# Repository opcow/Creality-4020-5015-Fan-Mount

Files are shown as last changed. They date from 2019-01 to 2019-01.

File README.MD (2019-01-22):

# Ender 3 4010/4020/5015 Fan Mount and Duct

---
### Main Cooling Fan Mount
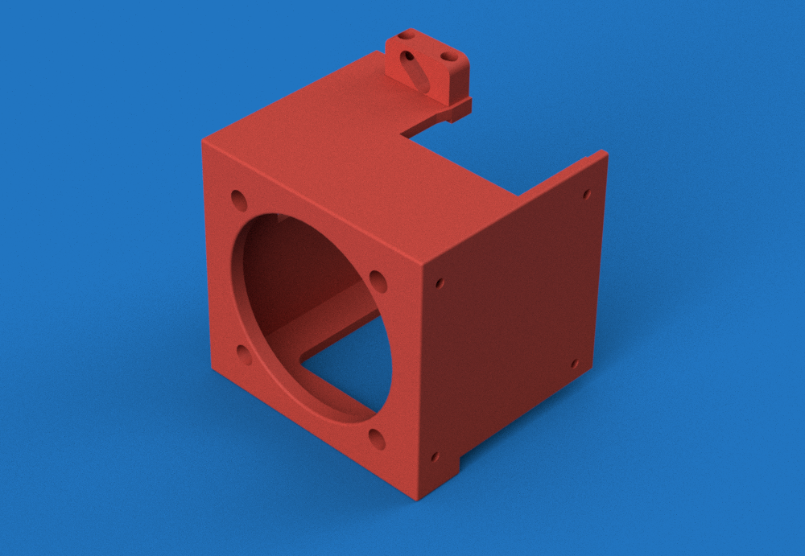
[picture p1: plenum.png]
plenum image


This part is based on the stock fan cover, but allows the use of a 4020 axial fan on Ender 3 and maybe other Creality printers for heatsink cooling. If using a 4020 fan it must mount on the outside. A 4010 fan should work mounted inside, but I haven't tried it. You can use the stock part cooler or the 5015 bracket and duct with this part (see below).

Parts needed:
* The stock heat sink cooling fan or another 4010 or 4020 axial fan. (The Ender 3 fans are 24v.)
* 2-4 M4 x 15-25mm screws depending on your fan size for mounting the fan. (I only use 2.)
* 4 M3 x 8-10MM screws.
* The original 2 M3 fan cover mounting screws or 2 more M3 x 6mm. If using a socket cap screw for the top bracket slot, a small washer may be needed.
* The original 4 part cooling fan screws or 4 M2 socket cap screws. I believe the stock screws are 2 8mm at the top and 2 10mm at the bottom (where the duct mounts).

Parts to print:

<ul>
<li>plenum_v2.stl</li>
<li>bracket_left_v2.stl</li>
<li>bracket_top_v2.stl or bracket_top_no_slot_v2.stl</li>
</ul>
  I designed this in multiple parts to avoid the need for supports. Print with the fan intake hole down. Be sure to print the left bracket with a flat side down. The non-slotted top bracket can be substitutted for the slotted version. The slotted version provides a bit of adjustment if the fan mount tilt.

Assembly:
1. Mount the top bracket to the fan housing using 2 M3 screws.
2. Mount the left bracket to the fan housing using the 2 stock M3 cover mounting screws or your own M3 screws.
3. If the screw holes are tight you may get bulges around them where the housing mounts to the metal bracket. If so, trim them and any other bumps using a razor of a file, so that the housing will mount flush with the metal plate.
4. Do the following 2 steps in whatever order works best for you. I Installed an inline connector for my 4020 fan, so I install it first and then plug it in as the last step.
5. Mount the fan to the fan housing. Make sure it is oriented so that it blows inward.
6. Mount the stock part cooling fan (don't forget its 90° duct) or the 5015 fan duct to the right side of the fan housing.
7. Mount the fan housing using M3 screws.

---

### 5015 Bracket and Duct
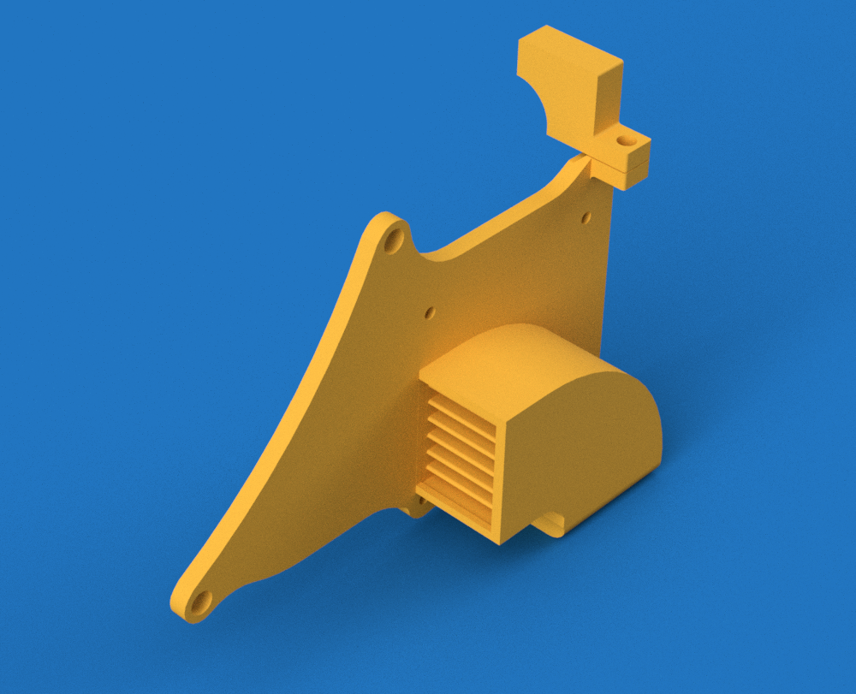
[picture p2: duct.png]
duct image

This part should also work with the stock metal fan cover. 

Parts needed:
* A 5015 centrifugal fan. (The Ender 3 fans are 24v.)
* 3 M2 screws (I used the screws for the stock part cooling fan for this).
* 1 M3 x 6-8mm screw if using the optional bracket.

Parts to print:
<ul>
<li>5015_duct_v2.stl or 5015_duct_v3.stl</li>
<li>5015_lower_duct_v3.stl or 5015_lower_duct_v3_mod.stl if using duct v3</li>
<li>duct_bracket_v2.stl</li>
</ul>

  5015_lower_duct_v3_mod.stl hangs lower and also angles the air a bit lower. 
  
  No supports are needed for the main part. The optional small bracket should be printed with supports and oriented with the slot facing upwards.

Assembly:
1. If you are using the printed main cooling fan mount, assemble it first as per above, but do not mount it to the printer.
2. Mount the duct to the right side of the main cooling fan box using 3 M2 screws.
3. Mount the entire assembly to the printer.

---
### Optional Items
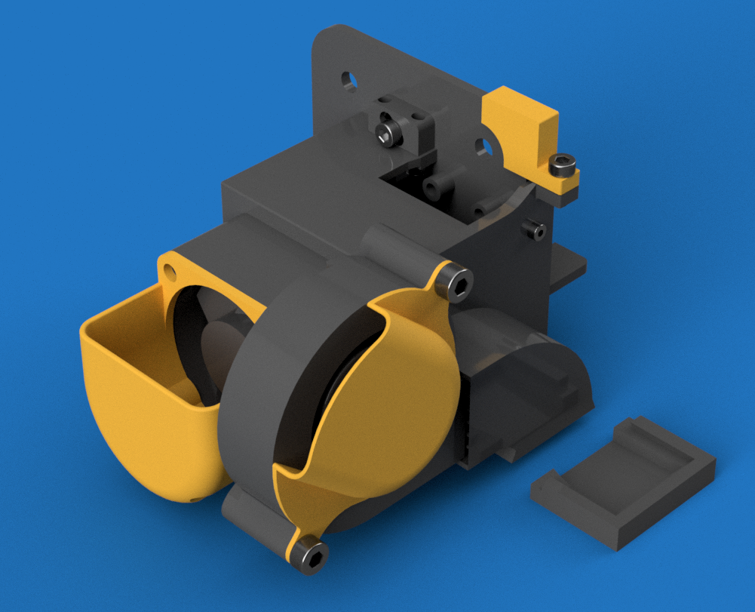
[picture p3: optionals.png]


 duct_bracket_v2.stl is an optional bracket that hooks to the hot end mounting plate. It gives the entire assembly a bit more stiffness. It won't work with the stock metal fan housing and would probably offer little to no benefit anyway.

 40_intake.stl and 50_intake.stl are optional intake ducts. They may reduce the amount of random plastic scrap getting sucked into the fans.

---
### Version 3 Duct

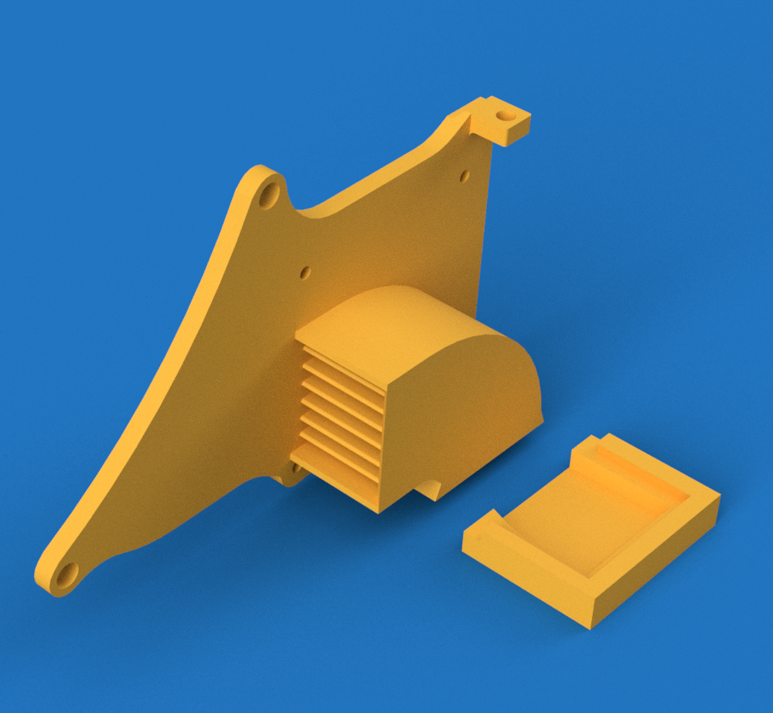
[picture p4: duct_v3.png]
duct version 3 image


Version 3 of the 5015 mount and duct uses a separate lower duct that snaps in using a dovetail joint. It may provide better airflow. Step files are included if you'd like to make your own modifications.

---

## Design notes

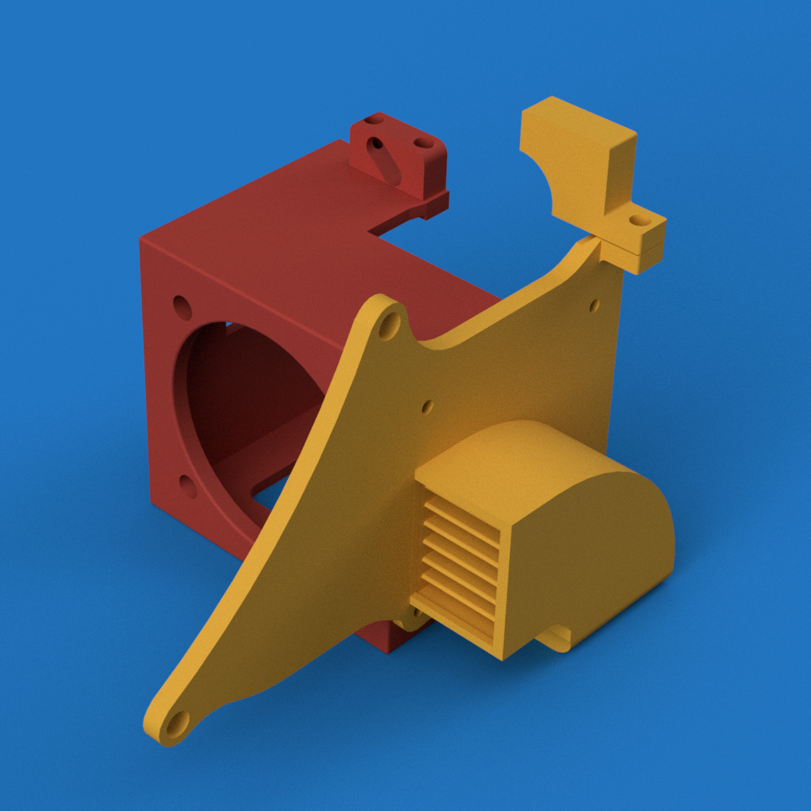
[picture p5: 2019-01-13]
view_5.png

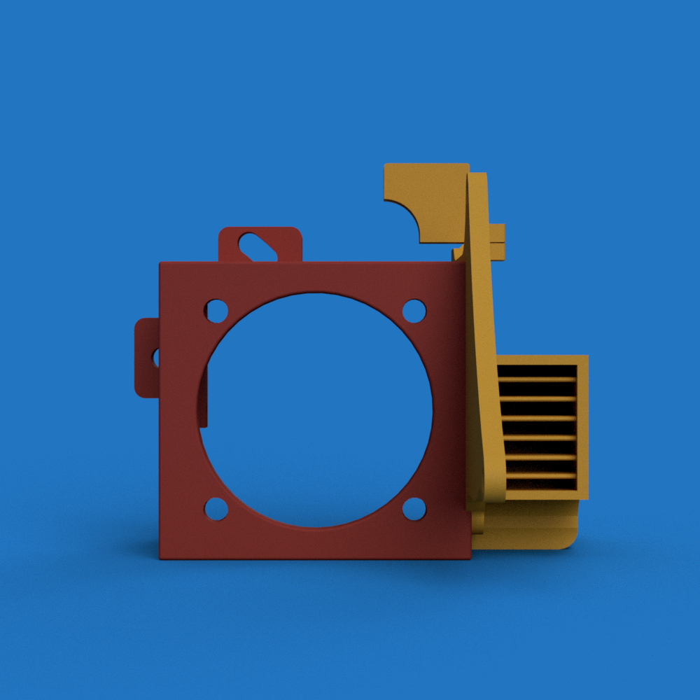
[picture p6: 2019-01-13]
view_3.png

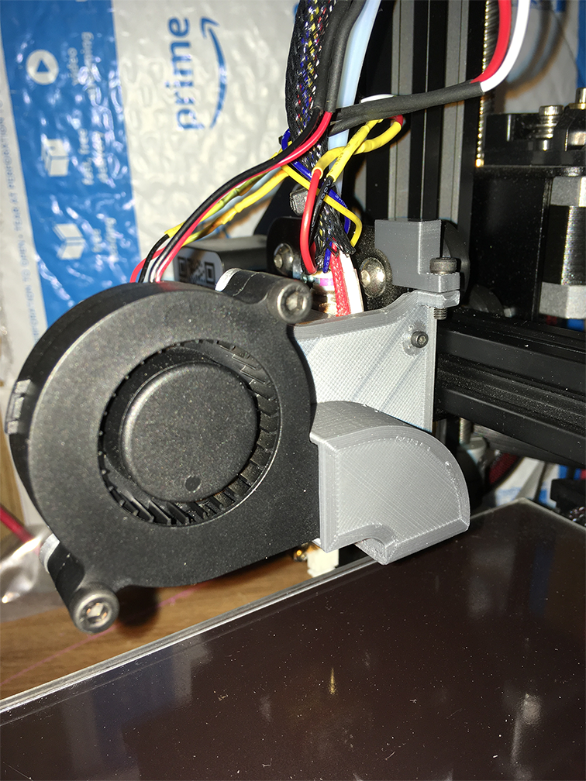
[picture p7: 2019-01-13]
snap.png

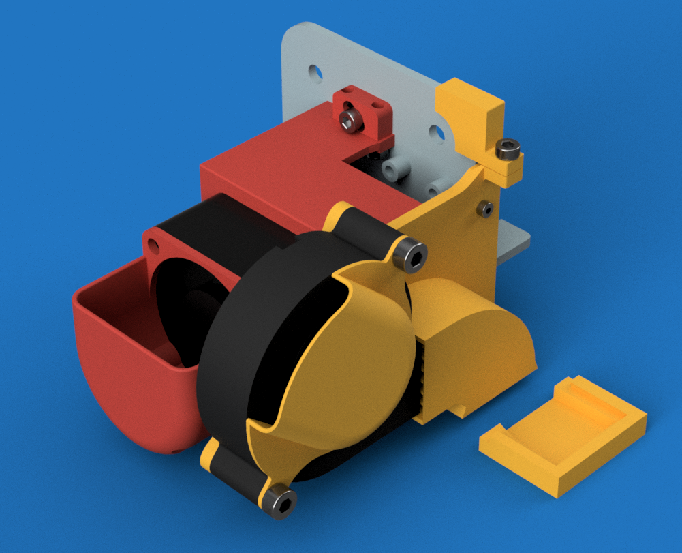
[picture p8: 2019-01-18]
view_1.png

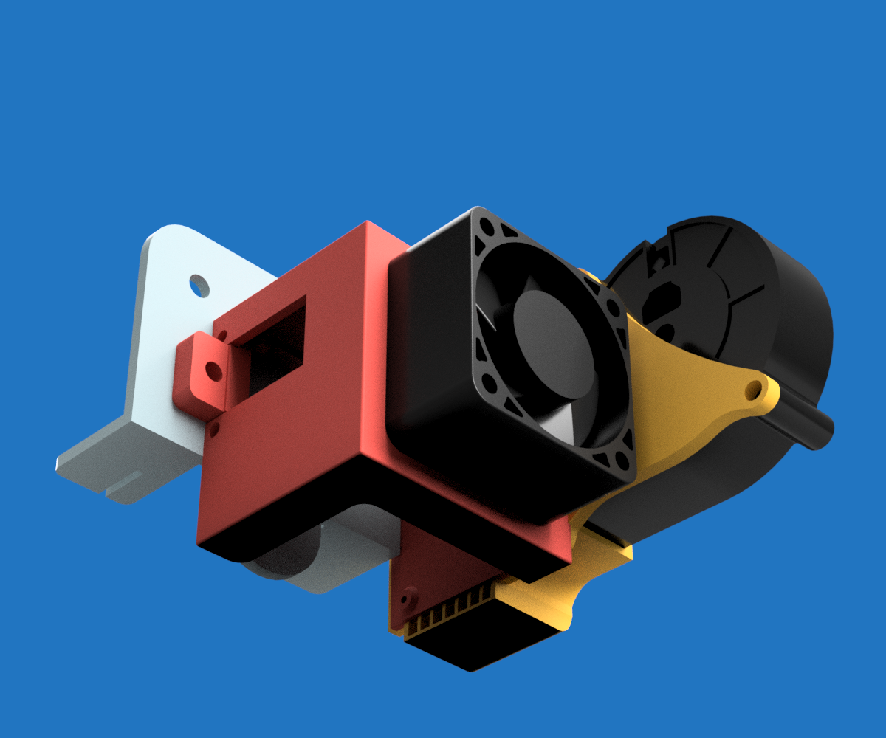
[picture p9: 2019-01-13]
view_2.png

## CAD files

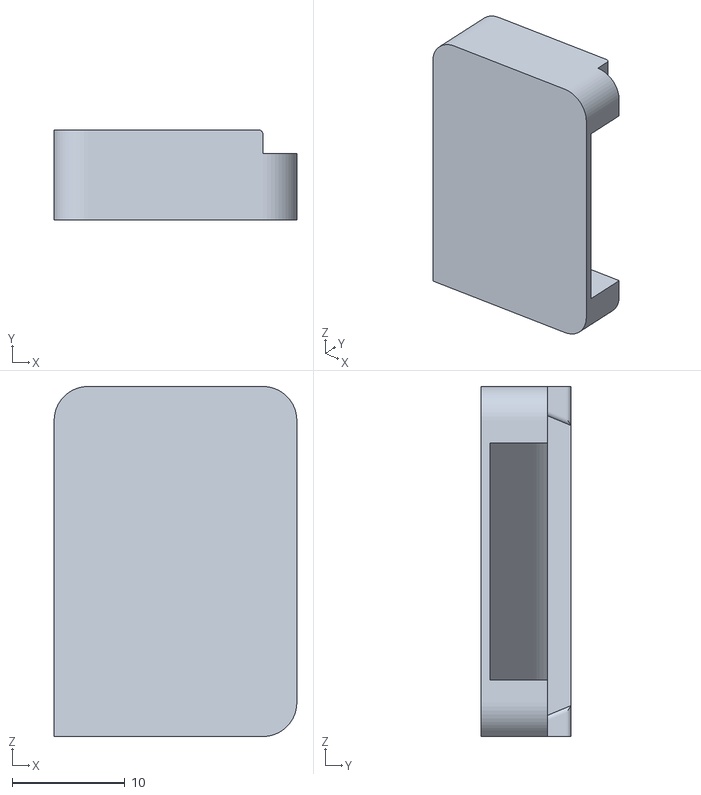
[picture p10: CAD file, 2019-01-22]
5015_lower_duct_v3_mod.stl
21.5 x 8.00 x 31.0

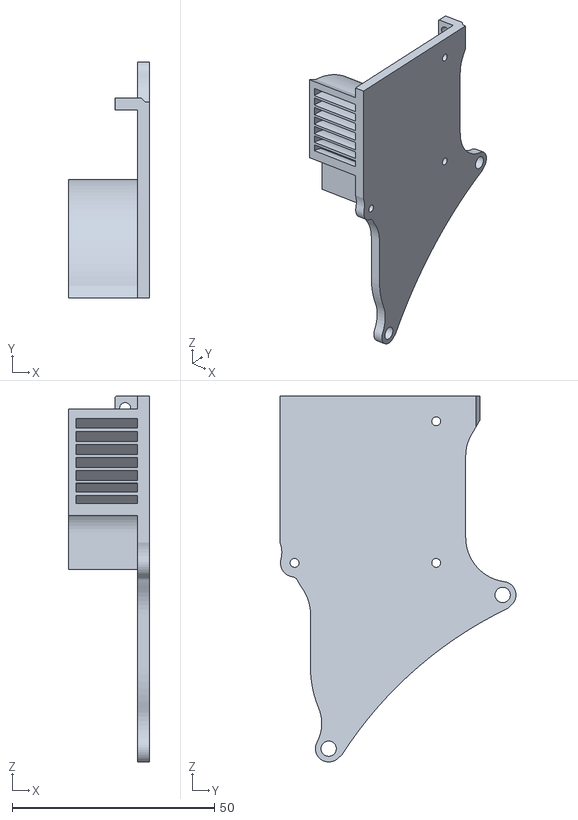
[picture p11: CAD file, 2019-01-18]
5015_duct_v3.stl
20.0 x 58.3 x 90.5

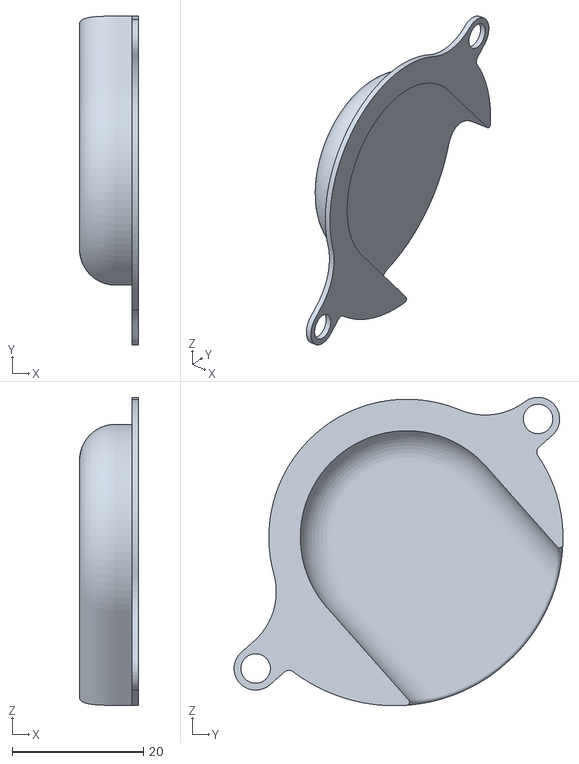
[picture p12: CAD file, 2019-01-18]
50_intake.stl
9.00 x 50.1 x 47.0

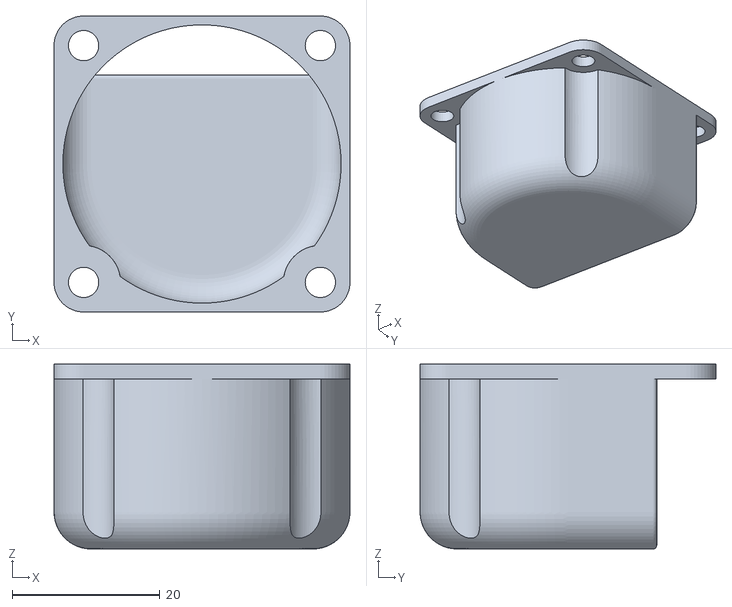
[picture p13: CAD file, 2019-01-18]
40_intake.stl
40.0 x 40.0 x 25.0

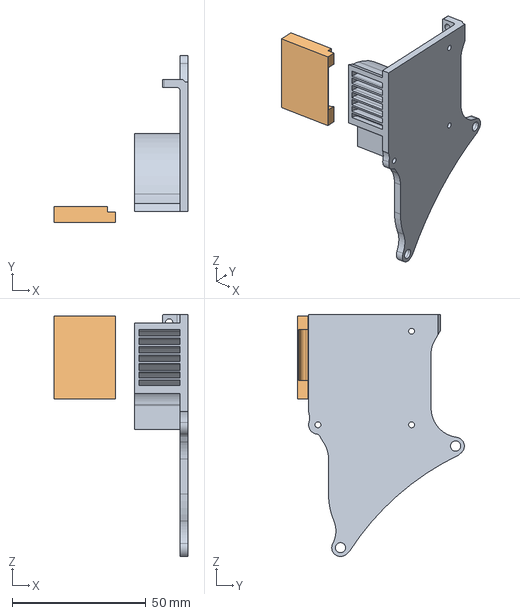
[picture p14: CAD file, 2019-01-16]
5015_Fan_Mount v3.step
50.0 x 62.3 x 90.5 mm

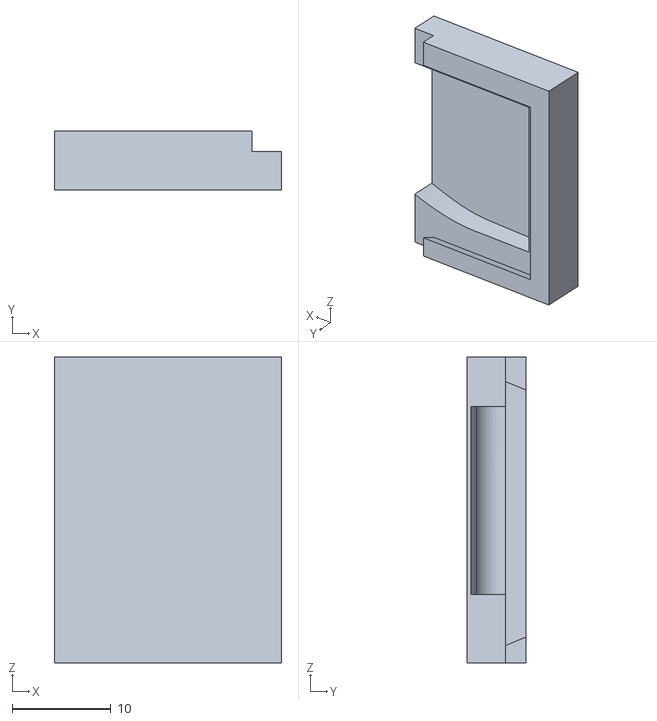
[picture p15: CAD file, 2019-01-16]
5015_lower_duct_v3.stl
23.0 x 6.00 x 31.0

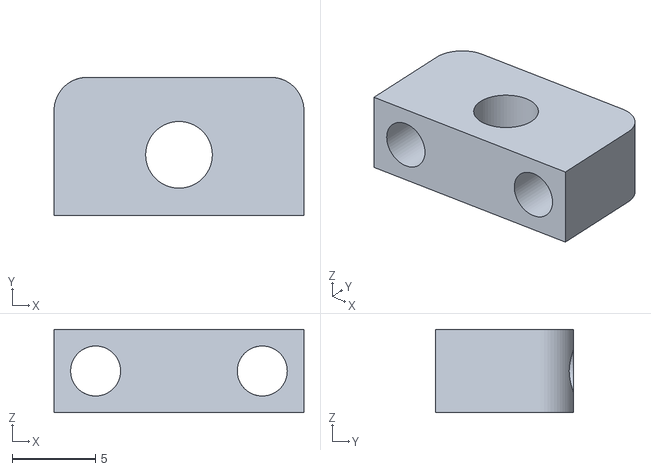
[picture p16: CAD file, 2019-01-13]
bracket_top_no_slot_v2.stl
15.0 x 8.30 x 5.00

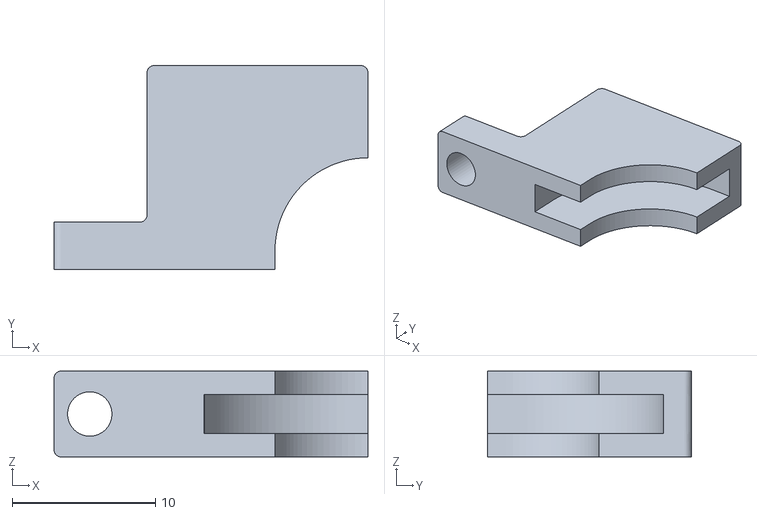
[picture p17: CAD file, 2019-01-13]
duct_bracket_v2.stl
21.9 x 14.2 x 6.00

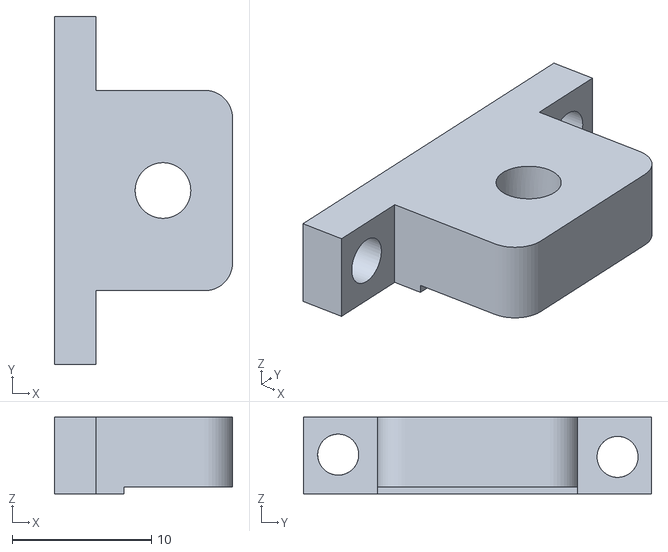
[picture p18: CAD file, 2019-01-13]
bracket_left_v2.stl
12.8 x 25.0 x 5.50

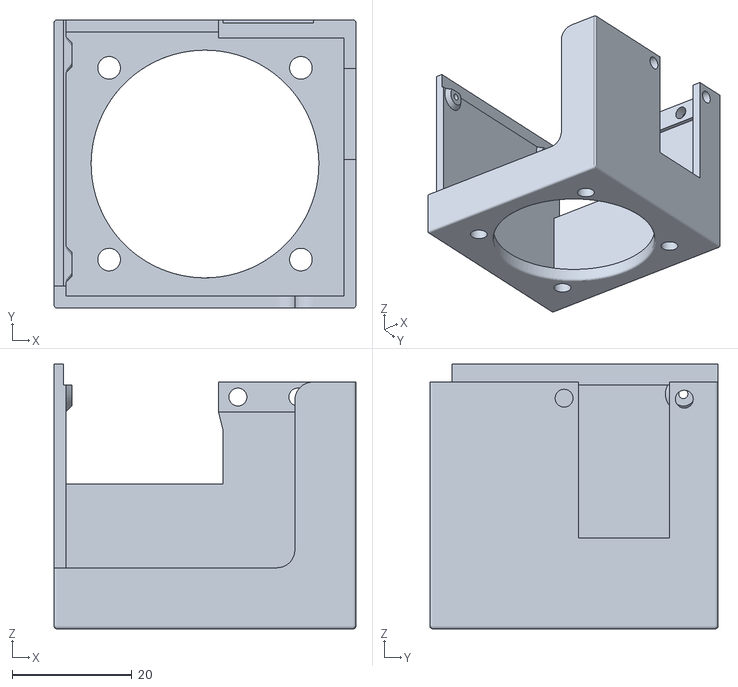
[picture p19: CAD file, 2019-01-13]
plenum_v2.stl
50.4 x 48.1 x 44.2

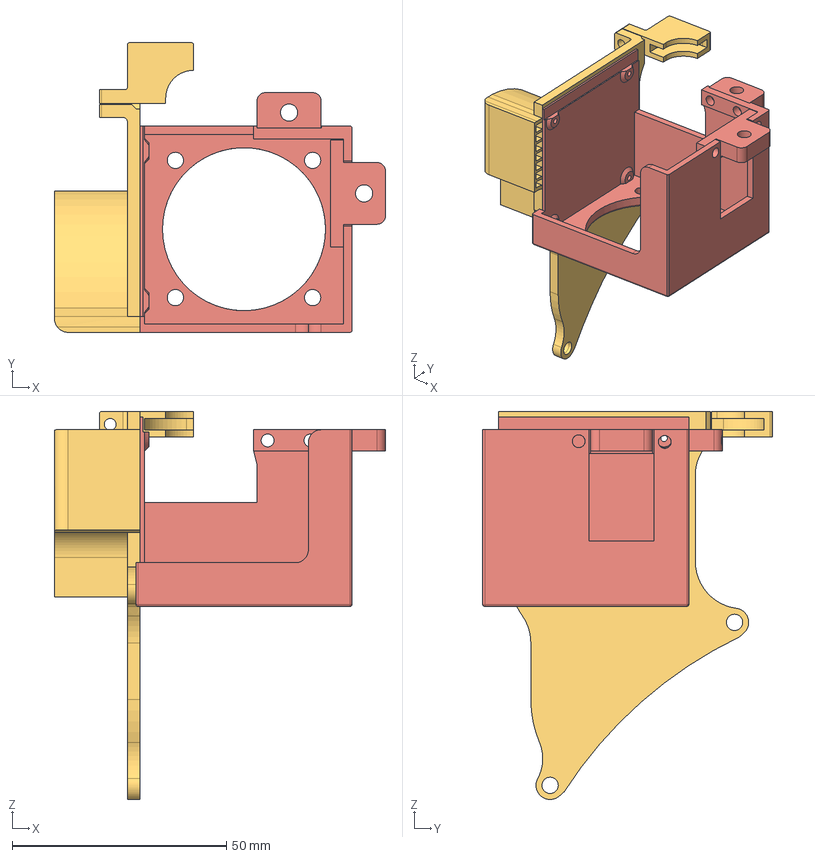
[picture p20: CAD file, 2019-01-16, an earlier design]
5015_Fan_Mount v2.step
77.2 x 67.5 x 90.5 mm

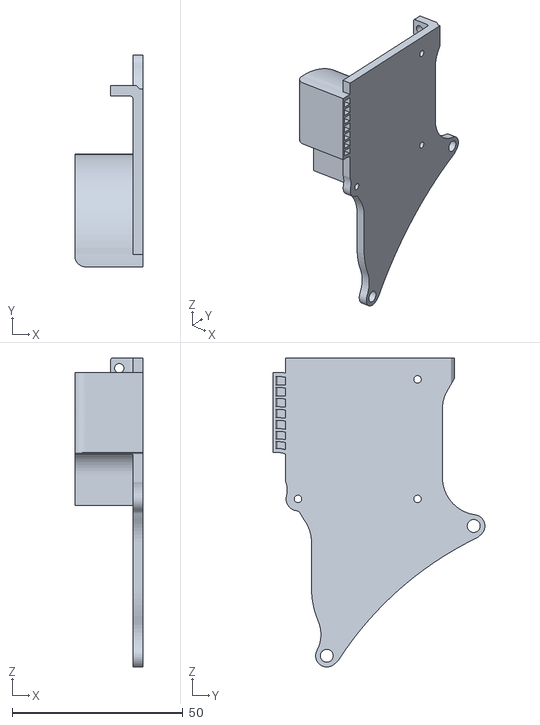
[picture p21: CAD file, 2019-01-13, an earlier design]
5015_duct_v2.stl
20.0 x 62.0 x 90.5

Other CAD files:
bracket_top_v2.stl

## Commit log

2019-01-13 clarification on screws
2019-01-13 new stl file
    [Bracket Top No Slot.stl]
2019-01-13 filename change
    [bracket_top_no_slot.stl]
2019-01-13 slotted bracket info
    [bracket_top_no_slot_v2.stl]
2019-01-16 version 3 files
    [5015_Fan_Mount v2.step, 5015_Fan_Mount v3.step, 5015_duct_v3.stl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]
2019-01-18 added screw
2019-01-18 shift bracket mount 1mm left
    [5015_duct_v3.stl]
2019-01-22 modified lower duct
    [5015_lower_duct_v3_mod.stl]
